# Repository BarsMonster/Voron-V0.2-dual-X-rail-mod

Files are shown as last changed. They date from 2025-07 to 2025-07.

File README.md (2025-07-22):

# Dual X-rail mod fo Voron v0.2 - released, v2


This is a successor to https://github.com/BarsMonster/Voron-V0-dual-rail-mini-aftersherpa

**Warning:** Mod to raise X rail by 4mm is missing for 0.2 at the moment, and only available for 0.1. If you find it or mod it yourself - please let me know. Reference from 0.1: https://github.com/camerony/VoronCustom/tree/main/V0.1_Raise_X_Axis_Extrusion_by_4mm

One of the limitations on the path to better print quality, higher accelerations, less ringing is rigidity of the printer. Weakest point in Voron V0 is arguably X-rail carriage. I believe that dual MGN7 offers more rigidity / less play than even single MGN9 rail due to less "amplification of backlash". In my view the only competing single-rail approach offering similar rigidity is [Pandora-style](https://github.com/MasturMynd/Pandora) rail mount on the front  with wide rail (MGW7 / MGW9) - but it requires significantly more changes to the printer.

This mod still requires raising X extrusion by 4mm by other mods.
It should be compatible with all v0.2 printheads, and especially [Dragon Burner](https://github.com/chirpy2605/voron/tree/main/V0/Dragon_Burner). 

# Variations
* X_Carriage_Support_dual_rail_wide_2mm_lower_x1.stl - **Main, recommended version.** Wider body for extra rigidity. Upper part is 2mm thinner, printhead mount point is lowered by 2mm. So your printhead is only 2mm higher than stock (taking into account X-rail being 4mm higher). Uses longer heat inserts instead of drop-in M3 nuts for printhead mounting. 3 heat inserts at the bottom to install "loop" mount of Dragon Burner as a 4th mount point of the printhead (optional) or other additional hardware.
* X_Carriage_Support_dual_rail_maxcompatible_x1 - upper part is exactly as stock v0.2, ensuring maximum possible compatibility, but raises printhead 4mm (due to higher X gantry).

# Travel range

* XY travel range is unaffected.
* Z travel range is increased 2mm (if allowed by Z-axis). You might need to shift Z rails up few mm if you don't reach Z=0mm level.
* Free space above carriage is reduced by 2mm, so you will benefit from any of tophat mods with more space (but stock v0.2 already has some extra space, so it is less critical).

# Requires

* Second 150mm MGN7 rail with MGN7H carriage, medium preload. I personally order custom 155mm ones to allow to mod for slightly larger X-travel range (for wiping e.t.c), otherwise standard 150mm one will do just fine.
* 10xM2 nuts and 10x M2x6mm screws to mount secondary rail, print 1x standard nut carrier.
* Mod to raise X rail by 4mm : TBD for v0.2, for v0.1 : https://github.com/camerony/VoronCustom/tree/main/V0.1_Raise_X_Axis_Extrusion_by_4mm
* 6x M2x5mm or M2x6mm screws to mount bottom rail. Recommended to get ultrathin ones, as it's quite tight on the bottom. If screws hit extrusions, and you only have regular hex screws - you can sand them down by ~0.5mm to make thinner head.
* 2-4x M3 heat inserts. "2mm_lower" version is also using 2 extra heat inserts for printhead mounting instead of sunk m3 nuts. You can use longer heat inserts (5-7mm) for printhead mounting for maximum strength - this will require the most care.

# Installation
* You might need to lower Z-axis extrusions ~1-2mm to the bottom to improve clearance.
* You will need to be more careful with wiring - as there is less space below printhead, but in good designs wiring is hidden & routed inside printhead.
* The most tricky part is matching distance between 2 X-rails. If you have small gap there due to 3d print or extrusion variation - don't sqeese carriage, as it will apply constant preload on the bearing blocks and will make it less smooth. If you have a gap >0.1mm - add spacers or scale carriage in Z direction slightly to fit snugly. In my case there was a gap of 0.3mm and I added a spacer.
* v0.2-style mount is more rigid than v0.1, so you might not need to do connection on the bottom 3 heat inserts, this is reserve for the future.

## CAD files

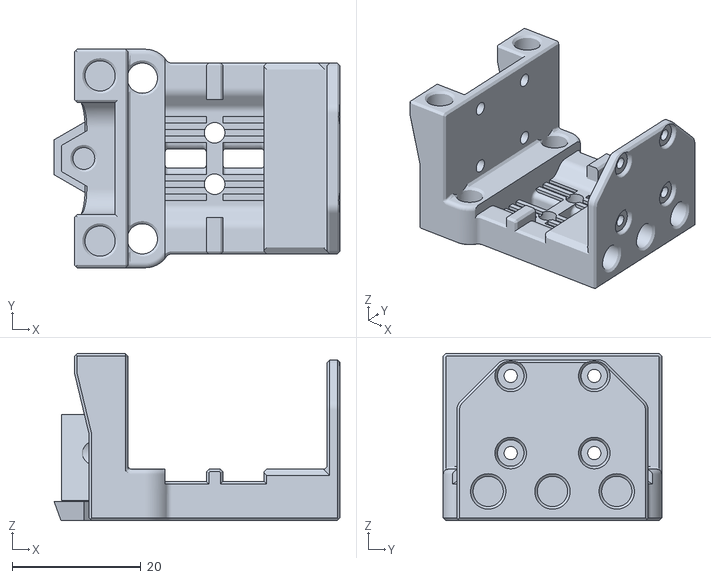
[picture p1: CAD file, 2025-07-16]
X_Carriage_Support_dual_rail_wide_2mm_lower_x1.stl
44.5 x 34.0 x 26.0

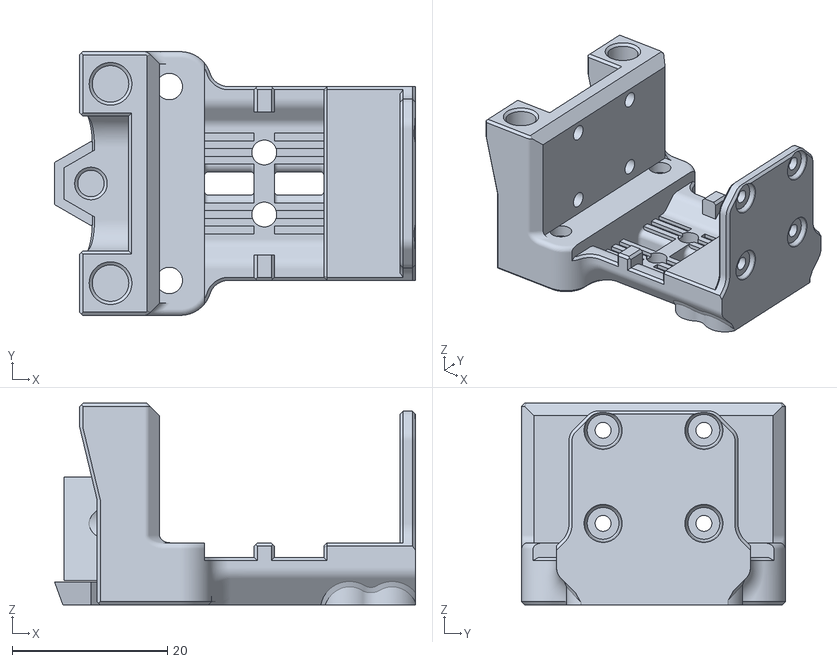
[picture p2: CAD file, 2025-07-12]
X_Carriage_Support_dual_rail_maxcompatible_x1.stl
46.6 x 34.0 x 26.0
